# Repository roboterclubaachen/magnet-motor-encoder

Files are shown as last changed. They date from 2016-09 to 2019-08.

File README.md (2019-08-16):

# magnet-motor-encoder

## board-as5045b_rev10

### Motorencoder für axial befestigten diametralen Magneten

Motor-Encoder mit ams AS5045B.

Der AS5045B ist ein IC welcher die Ausrichtung eines über ihm befindlichen Magneten mit 12 Bit Auflösung erfasst.

An der Motorachse muss ein Ø 6 mm x 2.5 mm Magnet mit diametraler Orientierung befestigt werden, die zulässige Toleranz betrögt 0.1 mm.
Das Magnet ist exakt mittig über dem IC (welcher mittig auf der Platine platziert ist) ausgerichtet werden, der Toleranzbereich beträgt hier 0.25mm.

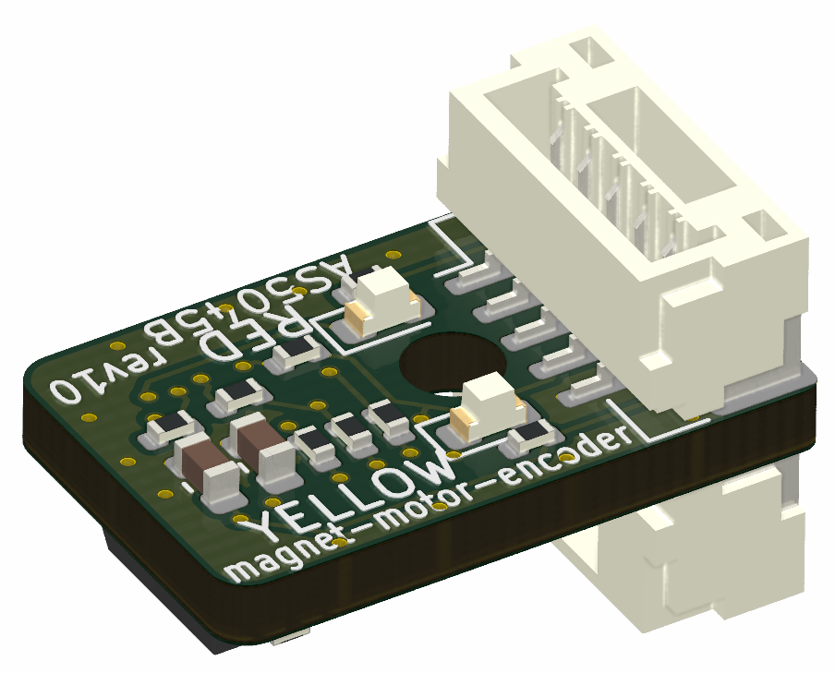
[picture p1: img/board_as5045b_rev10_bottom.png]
AS5045B rev10 Bottom

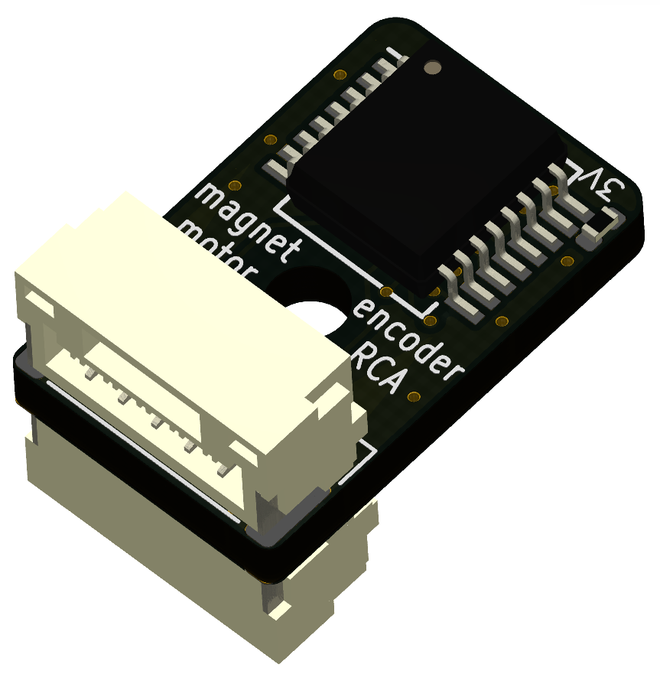
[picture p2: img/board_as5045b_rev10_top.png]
AS5045B rev10 Top


### Mechanische Dimensionen

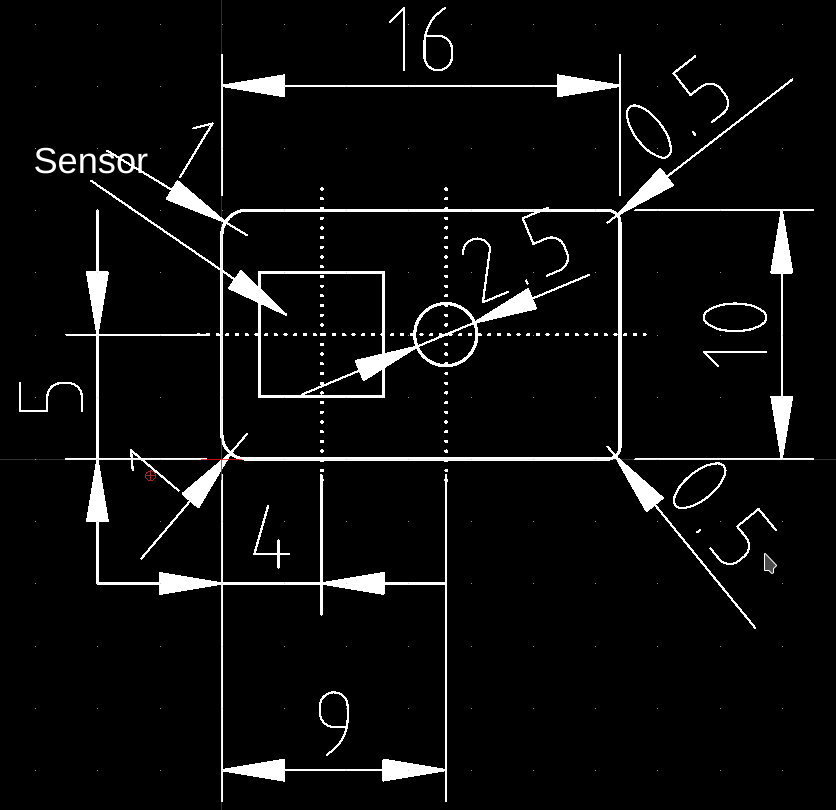
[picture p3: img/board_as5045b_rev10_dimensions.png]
AS5045B rev10 Dimensionen


Alle Angaben in Millimeter.

### Bauteile

Anzahl | Bauteil              | Bezeichnung / MPN
------ | -------------------- | -----------------------
1      | Magnetsensor IC      | AS5045B-ASSM
1      | Stecker Vorderseite  | [JST GH SM05B-GHS](https://www.digikey.de/product-detail/de/jst-sales-america-inc/SM05B-GHS-TB-LF-SN/455-1567-1-ND/807835) (1.25mm)
1      | Stecker Rückseite    | [JST GH BM05B-GHS](https://www.digikey.de/product-detail/de/jst-sales-america-inc/BM05B-GHS-TBT-LF-SN-N/455-1581-1-ND/807849) (1.25mm)
1      | LED Rot              | Bauform 0603
1      | LED Gelb             | Bauform 0603
2      | Vorwiderstand LED    | Bauform 0402
3 or 4 | Null-Ohm-Widerstand  | Bauform 0402
2      | Kondensator          | 2,2µF, >6,3V, X7R, Bauform 0603

### Stecker

Auf der Platine sind zwei 5-polige [JST GH](https://jst.de/product-family/show/89/gh) Stecker vorgesehen, welche Alternative bestückt werden können.
Der Stecker auf Vorderseite der Platine (wo auch der Sensor sitzt) bietet einen horizontalen Kabelausgang während auf der Rückseite ein vertikaler Kabelausgang vorgesehen ist.

Das Pinout beider Stecker ist identisch.

Pin | ABI-Interface | Serielles Interface
--- | ------------- | -------------------
 1  | A             | Data Out
 2  | +5V oder +3V3 | +5V oder +3V3
 3  | B             | Clock
 4  | I             | Chip Select (inverted)
 5  | GND           | GND

### Optionen / Konfiguration

#### Versorgungsspannung

Es sind sowohl 3,3V als auch 5V Versorgungsspannung möglich.
Die Versorgungsspannung muss mittels des einzigen Null-Ohm-Widerstands auf der Vorderseite (Beschriftung "3V") konfiguriert werden.

Spannung     | Null-Ohm-Widerstands (Beschriftung "3V")
------------ | ----------------------------------------
4,5V .. 5,5V | Nicht bestückt
3,0V .. 3,6V | Bestückt

#### Interface

Mittels Null-Ohm-Widerständen können wahlweise das ABI- oder das serielle Interface aktiviert werden.

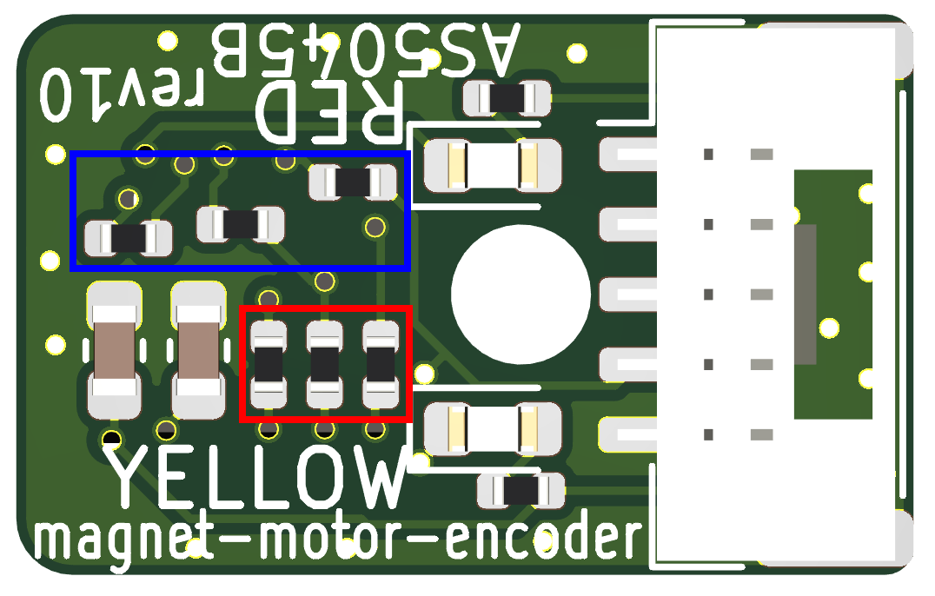
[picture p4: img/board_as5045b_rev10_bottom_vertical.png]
AS5045B rev10 Bottom Draufsicht


Zur Nutzung des ABI-Interfaces müssen die drei Null-Ohm-Widerstände innerhalb der blauen Markierung eingelötet werden.

Zur Aktivierung des seriellen Interfaces müssen die drei Null-Ohm-Widerstände innerhalb der roten Markierung eingelötet werden.

### Diagnose LEDs
* Rote und gelbe LEDs: Magnetfeldstärke
  * Aus: optimaler Betrieb
  * Gelb leuchtet: schwache Magnetfeldstärke, Magnet näher an IC platzieren.
  * Rot leuchtet: starke Magnetfeldstärke, Magnet weiter vom IC entfernt platzieren.
  * Rot und Gelb leuchten gleichzeitig: zu starkes oder zu schwaches Magnetfeld, keine zuverlässiger Betrieb möglich.

## board-as5045b

### Motorencoder für axial befestigten diametralen Magneten

Siehe [oben](#board-as5045b_rev10).

Die Platine ist hat exakt 22mm Durchmesser und sollte damit zu den *Namika* Motoren (ebenfalls 22mm Durchmesser) passen.
Das Magnet ist exakt mittig über dem IC, welcher mittig auf der Platine platziert ist, ausgerichtet werden.

### Diagnose LEDs
* Blaue LED: Power
* Rote und gelbe LEDs: Magnetfeldstärke
  * Aus: optimaler Betrieb
  * Gelb leuchtet: schwache Magnetfeldstärke, Magnet näher an IC platzieren.
  * Rot und Gelb leuchten: zu starkes oder zu schwaches Magnetfeld, keine zuverlässiger Betrieb möglich.

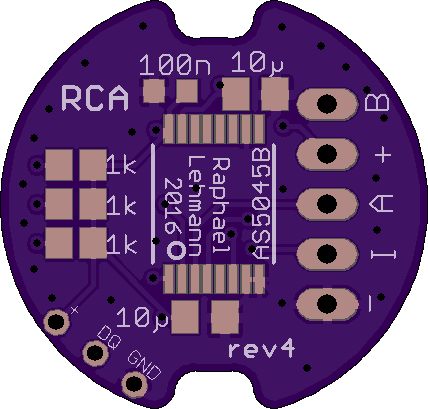
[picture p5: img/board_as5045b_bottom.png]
AS5045B Board Bottom

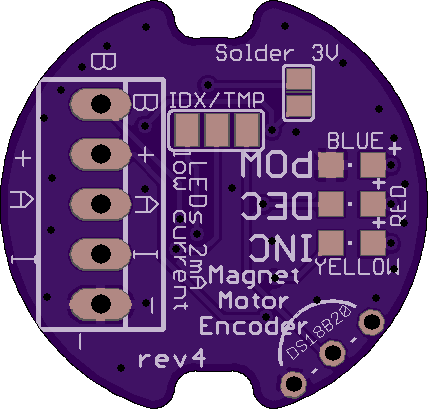
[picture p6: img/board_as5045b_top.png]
AS5045B Board Top


## board-as5304

### Motorencoder für axial befestigten mehrpoligen Ringmagneten

Motor-Encoder mit **ams** AS5304(A).

Der AS5304 ist ein IC welcher die Bewegung eines über ihm befindlichen mehrpoligen Magneten mit 160 Schritten pro Magnetpolpaar erfasst.
Die Platine ist hat etwa 12 mm Höhe und 39 mm Breite sowie ein 2mm Loch zu Ausrichtung über der Motorwelle.
Bei Bedarf kann dieses Loch aufgebohrt werden, in der Umgebung sind keine Leiterbahnen und kein Kupfer vorhanden.

An der Motorachse muss ein Ringmagnet mit 24 mm Innendurchmesser und 32 mm Außendurchmesser (-> MIttendurchmesser 28 mm) mittels eines nicht ferromagmetischen Werkstoffs befestigt werden.
Das Sensorarray im IC befindet sich exakt 28 mm vom Loch für die Motorachse entfernt, sodass die Platine bei Verwendung des oben genannten Magneten nur an der Motorachse und mit ca. 0.5 mm zum Ringmagnet ausgerichtet werden muss.

### Diagnose
* Blaue LED: Power
* Am Testpoint **AO** kann eine von der Magnetfeldstärke abhängige Spannung (gegen Testpoint **GND**) gemessen werden.

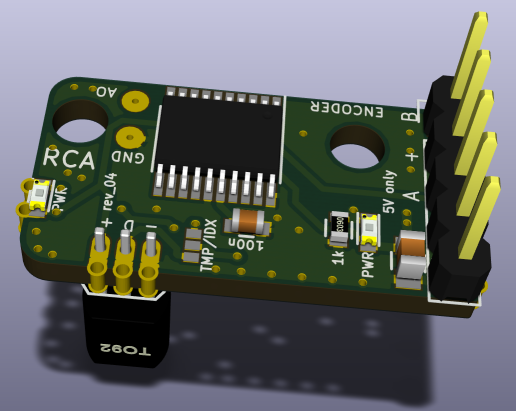
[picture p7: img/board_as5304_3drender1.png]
AS5304 Board 3D Ansicht (mit KiCad gerendert)

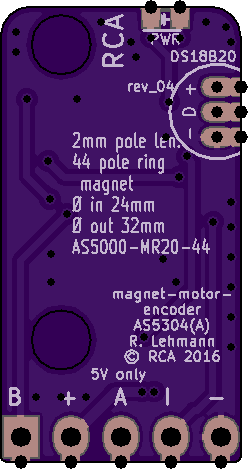
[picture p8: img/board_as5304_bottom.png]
AS5304 Board Bottom

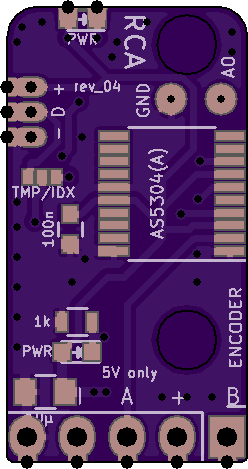
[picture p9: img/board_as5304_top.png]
AS5304 Board Top


## License

Copyright Raphael Lehmann 2016-2019

Licensed under CERN OHL v.1.2

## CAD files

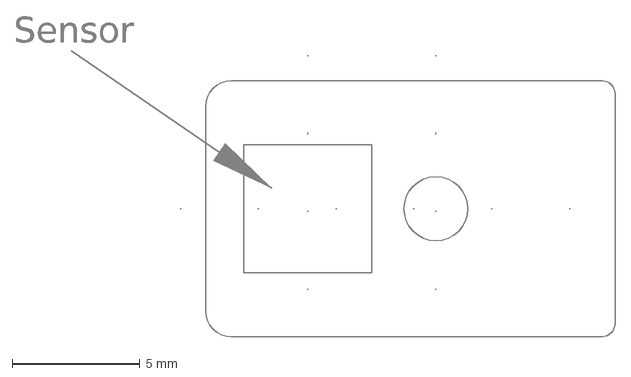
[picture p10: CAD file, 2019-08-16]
board-as5045b_rev10/dimensions.dxf
Sensor

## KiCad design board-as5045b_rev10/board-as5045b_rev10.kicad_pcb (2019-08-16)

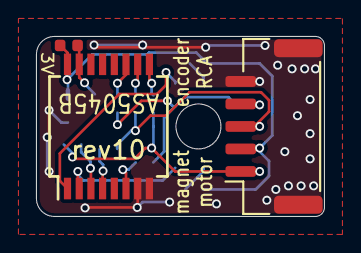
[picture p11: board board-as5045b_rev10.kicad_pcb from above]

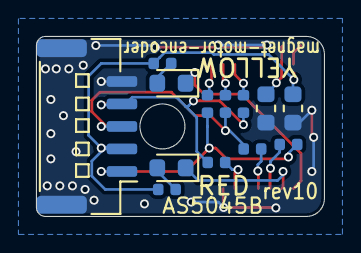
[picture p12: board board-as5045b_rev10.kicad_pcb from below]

Board: 2 copper layers, 16.0 x 10.0 mm, 16 parts (13 on the bottom side), 16 nets.

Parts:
C1, C2: 1µ 10V; C_0603_1608Metric
D1: YEL; LED_0603_1608Metric
D2: RED; LED_0603_1608Metric
J1: Connector_JST:JST_GH_BM05B-GHS-TBT_1x05-1MP_P1.25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; JST_GH_BM05B-GHS-TBT_1x05-1MP_P1.25mm_Vertical
J2: Connector_JST:JST_GH_SM05B-GHS-TB_1x05-1MP_P1.25m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; JST_GH_SM05B-GHS-TB_1x05-1MP_P1.25mm_Horizontal
JP1: 3V3; R_0402_1005Metric
R1, R2: 2k; R_0402_1005Metric
R3, R4, R5: 0; R_0402_1005Metric
R6, R7, R8: DNP; R_0402_1005Metric
U1: AS5045B; SSOP-16_5.3x6.2mm_P0.65mm

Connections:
+3V3: C2.1, JP1.2, U1.15
+5V: C1.1, J1.2, J2.2, JP1.1, R1.2, R2.2, U1.16
GND: C1.2, C2.2, J1.5, J1.MP, J2.5, J2.MP, U1.7, U1.8
unnamed: D1.1, U1.1
unnamed: D1.2, R1.1
unnamed: D2.1, U1.2
unnamed: D2.2, R2.1
unnamed: J1.1, J2.1, R3.1, R6.1
unnamed: J1.3, J2.3, R4.1, R7.1
unnamed: J1.4, J2.4, R5.1, R8.1
unnamed: R3.2, U1.3
unnamed: R4.2, U1.4
unnamed: R5.2, U1.6
unnamed: R6.2, U1.9
unnamed: R7.2, U1.10
unnamed: R8.2, U1.11

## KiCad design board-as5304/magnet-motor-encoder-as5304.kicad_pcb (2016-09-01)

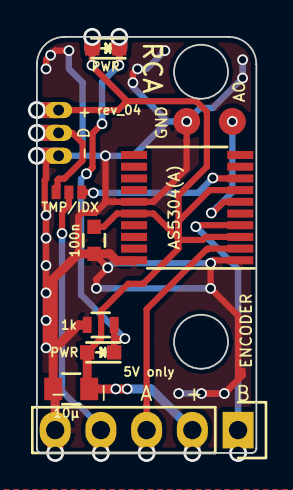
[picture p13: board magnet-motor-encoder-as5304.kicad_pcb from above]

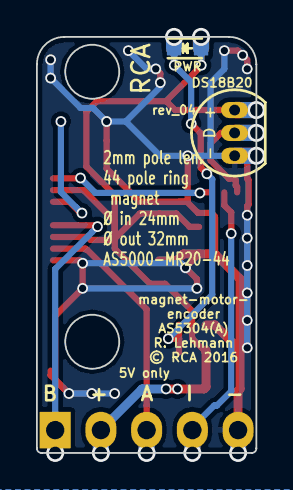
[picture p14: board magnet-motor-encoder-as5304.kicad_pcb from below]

Board: 2 copper layers, 12.2 x 23.1 mm, 12 parts (2 on the bottom side), 9 nets.

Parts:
C1: 100n; C_0603
C2: 10µ; C_0805
D1, D2, D2#2: PWR; LED_0603
JP1: ENCODER; Pin_Header_Straight_1x05
R1: 1k; R_0603
SJ1: TMP/IDX; S_JUMPER_3
U1: DS18B20; TO-92_Inline_Narrow_Oval
U2: AS5304(A); TSSOP-20_4.4x6.5mm_Pitch0.65mm
W1: GND; Measurement_Point_Round-SMD-Pad_Small
W2: AO; Measurement_Point_Round-SMD-Pad_Small

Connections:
+5V: C1.1, C2.1, D1.2, D2.2, D2#2.2, JP1.2, U1.3, U2.3, U2.7, U2.16
/A: JP1.3, U2.2
/AO: U2.6, W2.1
/B: JP1.1, U2.4
/IDX: SJ1.3, U2.8
/LED: D1.1, D2.1, D2#2.1, R1.1
/TMP: SJ1.1, U1.2
/TMP_IDX: JP1.4, SJ1.2
GND: C1.2, C2.2, JP1.5, R1.2, U1.1, U2.1, U2.15, U2.20, W1.1

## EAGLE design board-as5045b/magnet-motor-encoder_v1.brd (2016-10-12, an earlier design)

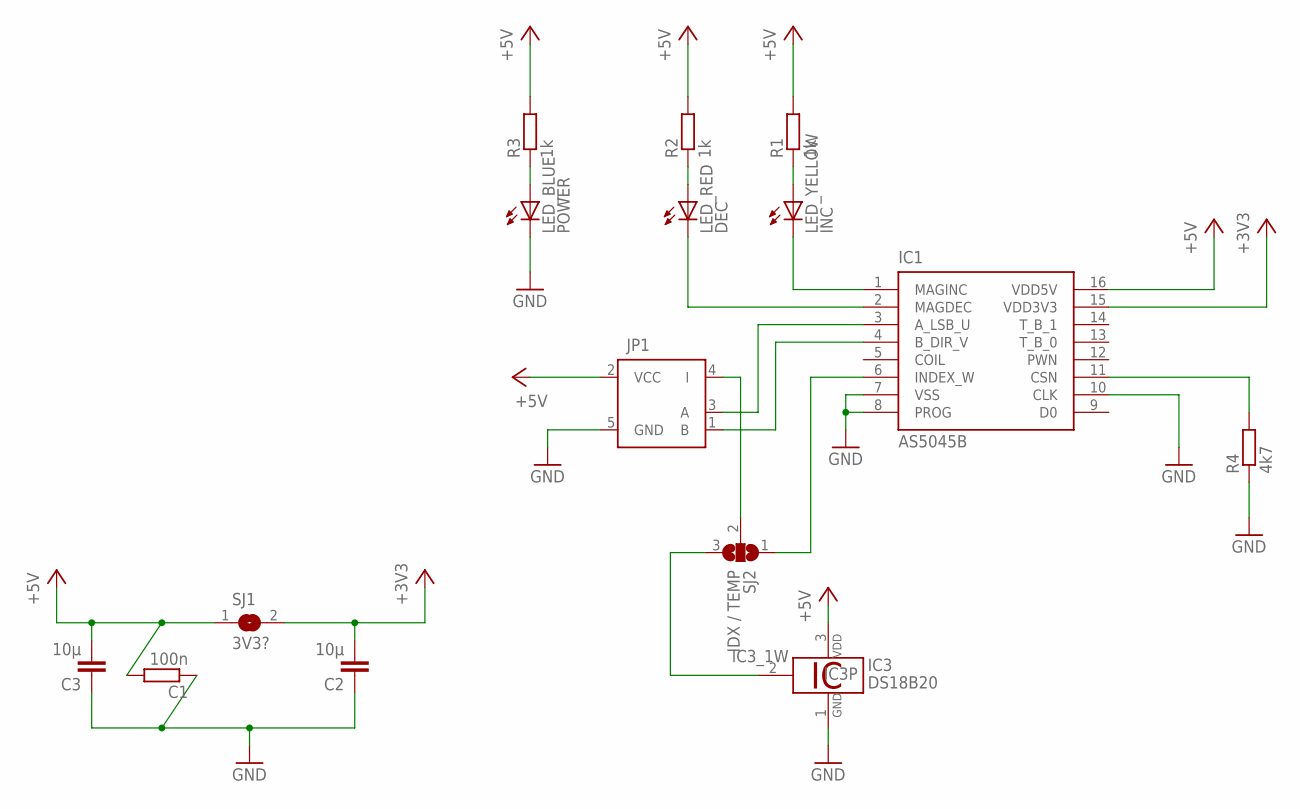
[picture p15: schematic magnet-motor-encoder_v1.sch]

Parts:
C1: 100n; R0603
C2, C3: 10µ; C0805K
IC1: AS5045B; SSOP16
IC3: DS18B20; TO92-
JP1: ENCODERPSS; 22-23-2051
LED_BLUE: POWER; CHIPLED_0805
LED_RED: DEC; CHIPLED_0805
LED_YELLOW: INC; CHIPLED_0805
R1, R2, R3: 1k; R0805
R4: 4k7; R0805
SJ1: 3V3?; SJS
SJ2: IDX / TEMP; SJ_2

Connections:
+3V3: C2.2, IC1.15 (VDD3V3), SJ1.2
+5V: C1.2, C3.2, IC1.16 (VDD5V), IC3.3 (VDD), JP1.2 (VCC), R1.2, R2.2, R3.2, SJ1.1
A: IC1.3 (A_LSB_U), JP1.3 (A)
B: IC1.4 (B_DIR_V), JP1.1 (B)
GND: C1.1, C2.1, C3.1, IC1.7 (VSS), IC1.8 (PROG), IC1.10 (CLK), IC3.1 (GND), JP1.5 (GND), LED_BLUE.C, R4.1
LED_RED: IC1.2 (MAGDEC), LED_RED.C
LED_YELLOW: IC1.1 (MAGINC), LED_YELLOW.C
unnamed: JP1.4 (I), SJ2.2
unnamed: IC1.6 (INDEX_W), SJ2.1
unnamed: IC3.2 (1W), SJ2.3
unnamed: IC1.11 (CSN), R4.2
R_LED_BLUE: LED_BLUE.A, R3.1
R_LED_RED: LED_RED.A, R2.1
R_LED_YELLOW: LED_YELLOW.A, R1.1

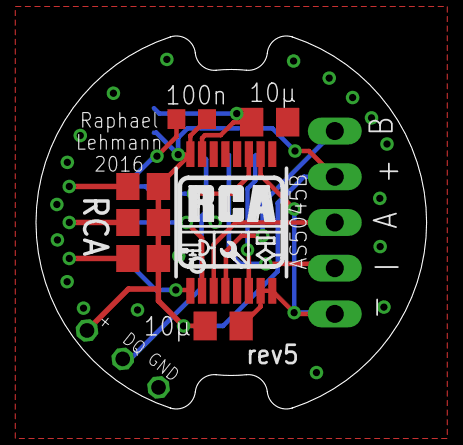
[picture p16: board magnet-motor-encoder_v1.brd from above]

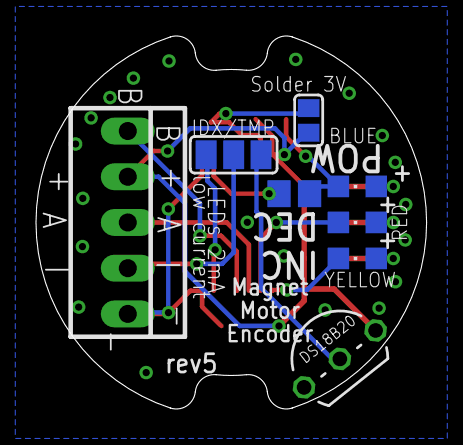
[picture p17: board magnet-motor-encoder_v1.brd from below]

Board: 2 copper layers, 21.7 x 20.7 mm, 16 parts (8 on the bottom side), 14 nets.

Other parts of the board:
U$1: LOGO_SILK

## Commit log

2016-07-04 inital board schematic and layout
    [magnet-motor-encoder_v1.brd, magnet-motor-encoder_v1.sch]
2016-07-04 board layout and silkscreen
    [magnet-motor-encoder_v1.brd, magnet-motor-encoder_v1.sch]
2016-07-04 board: silkscreen and ground vias
    [magnet-motor-encoder_v1.brd]
2016-07-04 board; adjust silkscreen
    [magnet-motor-encoder_v1.brd]
2016-07-06 board: add 1wire eagle library (LGPL)
2016-07-06 board: add DS18B20 temperature sensor (optional/uses encoder index pin signal)
    [magnet-motor-encoder_v1.brd, magnet-motor-encoder_v1.sch]
2016-07-06 board: adjust silk screen; add rev2 label
    [magnet-motor-encoder_v1.brd, magnet-motor-encoder_v1.sch]
2016-07-06 board: some minor fixes and improvements; rev3 label
    [magnet-motor-encoder_v1.brd]
2016-07-09 added magnet-motor-encoder-as5304 schematic (kicad) and kicad libs for solder jumper, as5304 and rca encoder psk
    [magnet-motor-encoder-as5304.kicad_pcb, magnet-motor-encoder-as5304.sch]
2016-07-09 remove kicad lib cache / extend gitignore
2016-07-09 board as5304: add AO and GND test points
    [magnet-motor-encoder-as5304.sch]
2016-07-10 board AS5304: add Power LED
    [magnet-motor-encoder-as5304.sch]
2016-07-10 KiCad lib solder jumper: Pins changed to passive
2016-07-10 board as5304: modified solder jumper; ERC passed
    [magnet-motor-encoder-as5304.sch]
2016-07-10 kicad lib: add open-project kicad footprint lib
2016-07-10 board as5304: footprints selected, netlist created
    [magnet-motor-encoder-as5304.sch]
2016-07-10 board as5304: add test point library; replace measurement point footprint
    [magnet-motor-encoder-as5304.sch]
2016-07-10 board as5304: add lib bjh-kicad-mountingholes-fp
2016-07-10 board as5304: create pcb layout
    [magnet-motor-encoder-as5304.kicad_pcb]
2016-07-10 board as5304: remove generated netlist file
2016-07-10 board as5304: replaced absolute libary paths
2016-07-10 board as5304: named signals in schematic
    [magnet-motor-encoder-as5304.sch]
2016-07-10 board as5304: fix component values
    [magnet-motor-encoder-as5304.sch]
2016-07-10 board as5304: finish pcb layout and silkscreen
    [magnet-motor-encoder-as5304.kicad_pcb]
2016-07-10 board as5045b: integrate mounting holes in board outline
    [magnet-motor-encoder_v1.brd]
2016-07-10 renamed board directories
    [magnet-motor-encoder-as5304.kicad_pcb, magnet-motor-encoder-as5304.sch, magnet-motor-encoder_v1.brd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]
2016-07-10 add as5304 board and images to README
2016-07-26 board as5304: rearrange components
    [magnet-motor-encoder-as5304.kicad_pcb]
2016-07-31 board as5304: replace bjh-kicad-mountingholes-fp with own fork
2016-07-31 board as5304: finish pcb layout and silkscreen for rev_02
    [magnet-motor-encoder-as5304.kicad_pcb]
2016-08-09 board as5304: replace most 0805 Rs and Cs with 0603 packages
    [magnet-motor-encoder-as5304.kicad_pcb, magnet-motor-encoder-as5304.sch]
2016-08-09 board as5304: update README images
2016-09-01 board as5045b: new board shape (imported from 3d-model/solidworks); rev4 tag
    [magnet-motor-encoder_v1.brd, magnet-motor-encoder_v1.sch]
2016-09-01 board as5304: new board shape (imported from 3d-model/solidworks); rev_04 tag
    [magnet-motor-encoder-as5304.kicad_pcb, magnet-motor-encoder-as5304.sch]
2016-09-20 board as5045b: moved backside resistors; new rev4 tag
    [magnet-motor-encoder_v1.brd]
2016-10-12 board as5045b: add missing CSn pulldown resistor; new rev5 tag
    [magnet-motor-encoder_v1.brd, magnet-motor-encoder_v1.sch]
2019-08-16 Add new board as5045b_rev10
    [board-as5045b_rev10.kicad_pcb, board-as5045b_rev10.sch, dimensions.dxf]

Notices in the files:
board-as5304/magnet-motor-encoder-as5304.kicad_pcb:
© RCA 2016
